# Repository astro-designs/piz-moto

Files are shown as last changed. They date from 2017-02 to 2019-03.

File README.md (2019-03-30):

PiZMoto
=======
A code library for the PiZ-Moto / PiZ-Moto+ add-on board for the Raspberry Pi Zero
with assembly instructions, examples for both Python & Scratch, tutorials,
and a 3D printable design for a Raspberry Pi Zero powered MicroPiNoon compatible balloon-popping 'bot!

The PiZ-Moto is a self-assembly simple 2-channel motor controller with extras...
   * On-board 5V power supply to power the Raspberry Pi Zero from the motor power supply
   * 3-pin connector for adding an infra-red reflective 'Line Follower' sensor
   * 4-pin connector for adding a HC-SR04 ultra-sonic distance sensor
   * 2 x 3-pin servo-compatible connectors usable as inputs or outputs (for LEDs, servos, etc.)
   * on-board GPIO driven LED
   * Expansion header bringing out some spare GPIO
   * Compatible with the CamJam EduKit-3 available from www.thepihut.com

Installation instructions for the Raspberry Pi
**********************************************

These instructions assume you are using the latest version of Raspbian and have logged in as user "pi"
Last tested with Raspbian Stretch 2017-09-07

1) Run git clone to clone the piz-moto folder to users/pi

   cd ~
   
   git clone https://github.com/astro-designs/piz-moto.git
   
2) Run the setup program

   sudo python setup.py install
   
This completes the basic installation.

Using a PS3-compatible wireless controller
******************************************

These setup notes are based on: https://www.piborg.org/blog/rpi-ps3-help

sudo apt-get update

sudo apt-get -y install libusb-dev joystick python-pygame

cd ~

wget http://www.pabr.org/sixlinux/sixpair.c

gcc -o sixpair sixpair.c -lusb

Tested with a Rock Candy wireless PS3 controller and one other ultra-cheap wireless PS3 controller found on ebay.

If you're looking for a wireless PS3 controller, this is also worth a look, available from The PiHut although i've not tested it myself...
https://thepihut.com/products/raspberry-pi-compatible-wireless-gamepad-controller

Documentation
*************

Assembly instructions: 
                     docs/PiZ-Moto+ Instructions.pdf (Instructions for PiZ-Moto+ (black)
                     docs/PiZ-Moto Instructions.pdf (Instructions for PiZ-Moto (green)

Example Code
************
examples/ps3bot.py - Simple 2-wheeled robot controller using a wireless PS3 controller

examples/wiibot.py - Simple 2-wheeled robot controller using a Bluetooth WiiMote controller
                     Includes routines to follow lines using an infra-red reflective sensor
                     and avoid objects using a HC-SR04 range sensor
                     
examples/candle.py - Using a PiZ-Moto motor driver to drive a lamp to simulate a flickering candle
                     
examples/Scratch/EduKitRobot.sb - Scratch based example,
                     Ideal for getting to grips with motor control using Scratch on the Raspberry Pi
                     VNC into your Raspberry Pi & PiZ-Moto and run Scratch over VNC to control your robot
                     instead of using a PS3 or Wii controller

Tutorials
*********

These tutorials were written for a simple motor control tutorial held at the Cotswold Raspberry Jam
in June 2017. The tutorial worksheet can be downloaded from:
http://cotswoldjam.org/downloads/2017-06/motor-control-worksheet.pdf

tutorial/task1.py
tutorial/task2.py
tutorial/task3.py

3D Printable MicroPiNoon 'Bot
*****************************

We've included all files, including STL files and the Sketchup model for our 3D-printed MicroPiNoon
MicroPiNoon compatible balloon-popping robots. These are a regular feature at the Cotswold Raspberry Jam

MicroPiNoon/3D_Printing         - stl files
MicroPiNoon/Bot4.jpg            - Simple render of the completed robot
MicroPiNoon/Instructions.txt    - Assembly instructions
MicroPiNoon/PartsList.txt       - List of parts needed for the robot

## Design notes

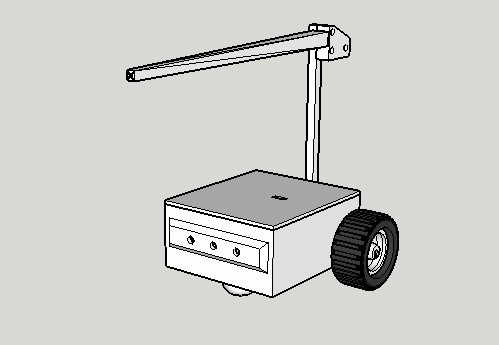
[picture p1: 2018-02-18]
MicroPiNoon/Bot4.jpg

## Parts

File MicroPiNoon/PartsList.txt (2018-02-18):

Parts list for Micro-Pi Noon fighting robot
*******************************************

1) Raspberry Pi Zero, Zero W, Zero WH Note: Header needs to be fitted. (Works with any revision / version)
2) PiZ-Moto motor controller board / kit;
3) Motors - 50:1 or 298:1 micro geared 6V motor.
   https://shop.pimoroni.com/products/micro-metal-gearmotor-extended-back-shaft
   or similar
4) PP3 Battery clip with wires attached
   https://shop.pimoroni.com/products/pp3-battery-snap
   or similar
5) Battery holder
   http://uk.farnell.com/keystone/2476/battery-holder-a-aa-snap-in/dp/2293271?st=aa%20battery%20holder%204
   or similar
6) M3 x 20 pan head screw (x4)
7) M3 full nut (x4)
8) A pin
   approx 20mm long with the head cut off. A small cork is recommended for safety...
9) Wheels - Polulo are good for these:
   https://shop.pimoroni.com/products/pololu-wheel-42x19mm-pair
   https://shop.pimoroni.com/products/moon-buggy-wheels-pair
   https://shop.pimoroni.com/products/pololu-wheel-32x7mm-pair
10) 8GB micro SD Card
11) Wireless PS3 controller
    Rock Candy or similar work well.

Note:
You will also need:

Insulated wire to solder to the micro motors.
   About 4 lengths of 10cm, preferably two in one colour and two in a different colour
   More may be needed if you opt for using a switch (see optional items below) to switch the power on/off.

3D printed parts:
*****************

1) BOT4 Chassis.stl - This is the main chassis;
2) BallFoot.stl - This is the non-rotating simple ball-castor alternative used to support the front of the 'bot';
3) BalloonMast.stl - this is the pole at the back of the bot that holds the baloon;
4) BalloonHolder.stl - this is the quick-release balloon holder;
5) Spike - this is the arm that extends forward over the 'bot' and carries the pin;
6) SpikeHolder.stl - this is a small clamp that holds the spike and baloon holder onto the baloon mast;
7) Bot4_Lid.stl - this is a simple clip-on lid that can act as a cover over everything. 

Optional:
a) Polulo #953 metal ball-castor. Optional replacement for 3D printed solid non-moving front 'foot'
   https://shop.pimoroni.com/products/pololu-ball-caster-with-3-4-metal-ball

b) Sliding power switch
   http://uk.farnell.com/knitter-switch/mfs131d/switch-spdt-0-35a-30vdc-solder/dp/219459?st=Slide%20switch
   or similar (check dimensions match the slide switch hole on the 'BOT4' 3D printed chassis

Tools required:
***************

1) Soldering iron - a good one with a fine tip. Suitable for lead-free solder
   Lead-free solder. Reasonably fine 0.5mm - 1mm

2) Screwdrivers to match the screws used
3) M3 spanner or nut-spinner - or a pair of pliers...
3) Cutters, pliers

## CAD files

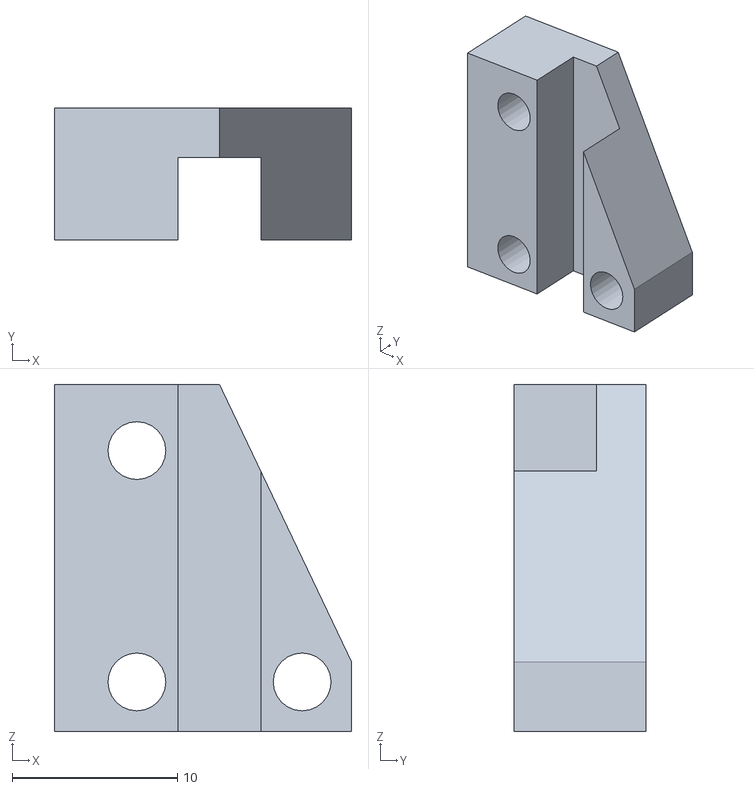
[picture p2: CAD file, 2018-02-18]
MicroPiNoon/3D_Printing/SpikeHolder.stl
18.0 x 8.00 x 21.0

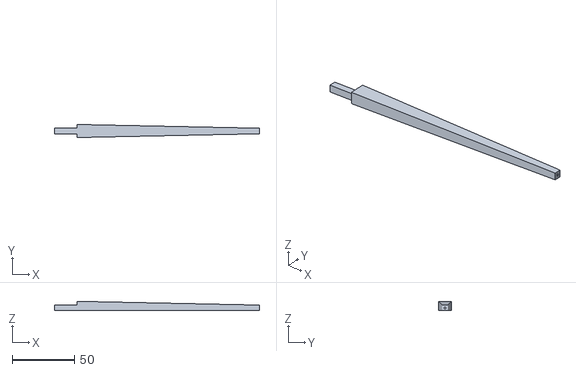
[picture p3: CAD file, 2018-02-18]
MicroPiNoon/3D_Printing/Spike.stl
165.0 x 10.5 x 7.50

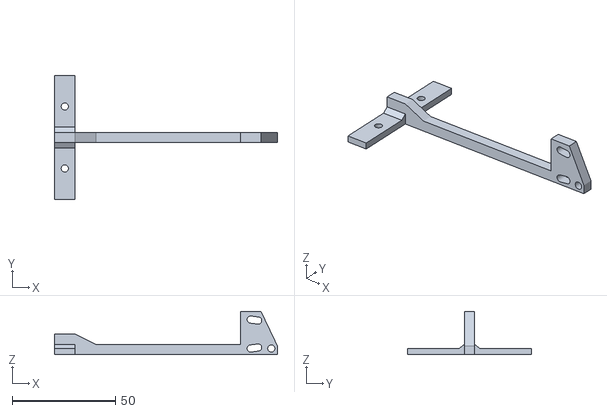
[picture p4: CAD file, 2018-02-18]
MicroPiNoon/3D_Printing/BalloonMast.stl
108.0 x 60.0 x 21.0

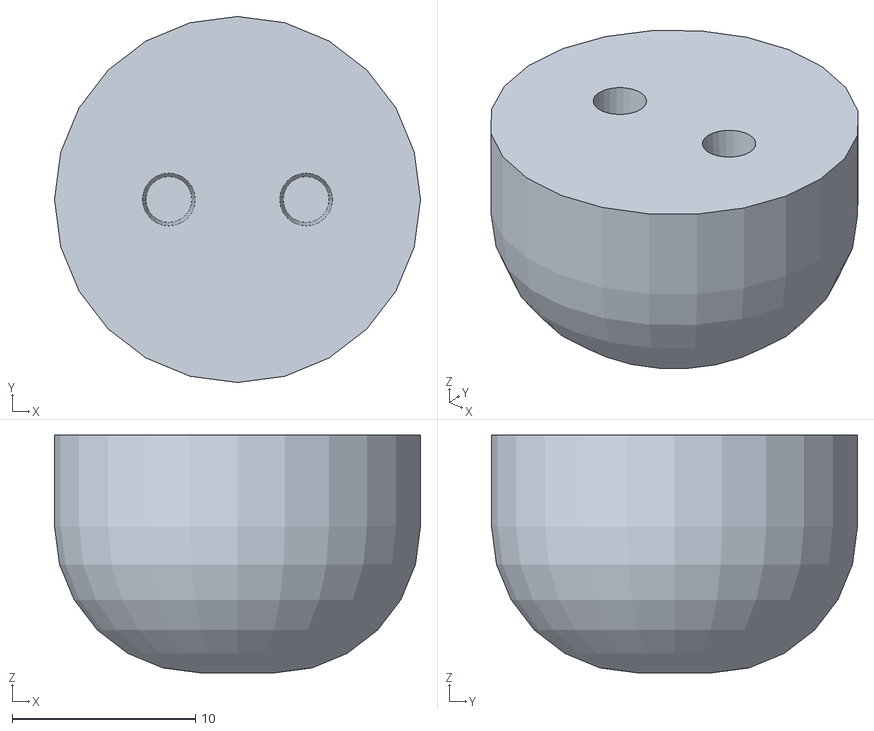
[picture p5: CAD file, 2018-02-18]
MicroPiNoon/3D_Printing/BallFoot.stl
20.0 x 20.0 x 13.0

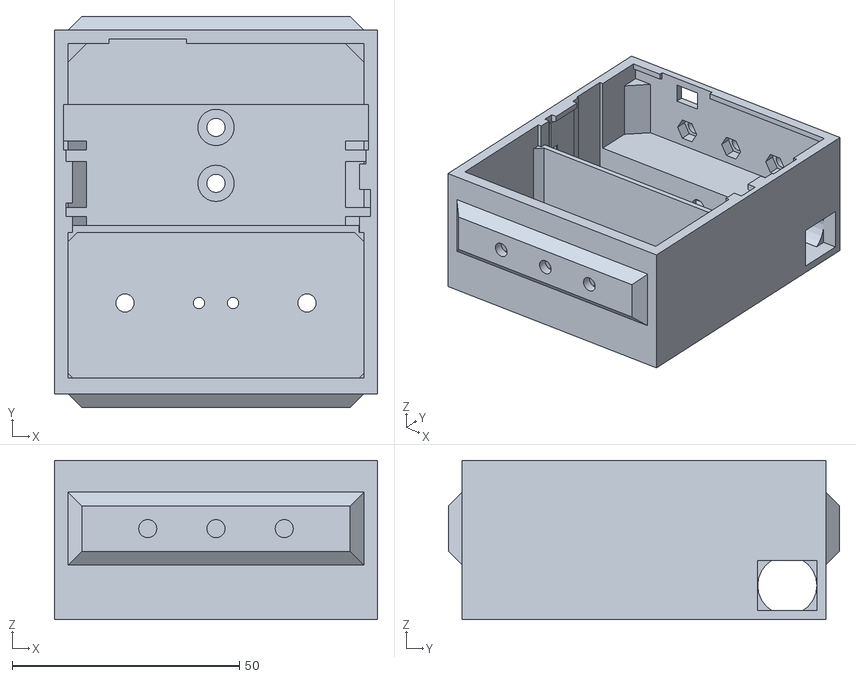
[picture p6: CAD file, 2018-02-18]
MicroPiNoon/3D_Printing/Bot4Chassis.stl
71.0 x 86.0 x 35.0

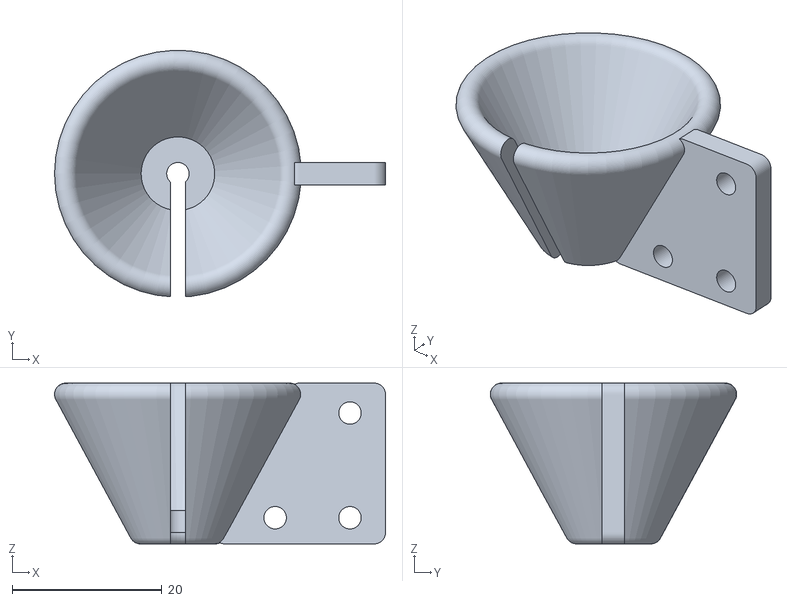
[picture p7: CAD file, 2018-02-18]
MicroPiNoon/3D_Printing/BalloonHolder.stl
44.2 x 32.9 x 21.5

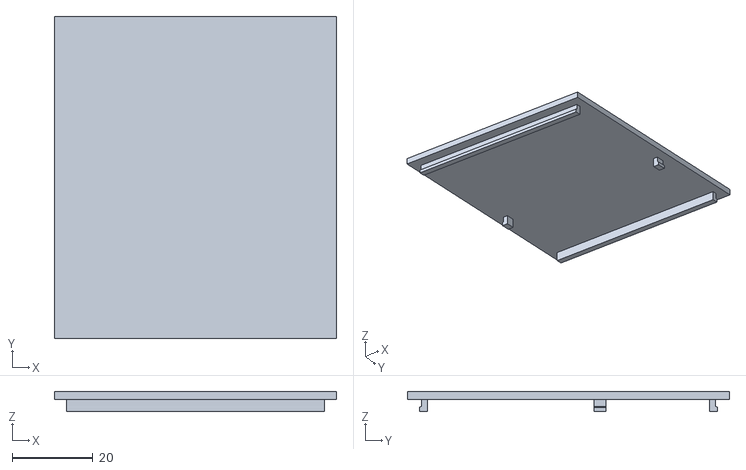
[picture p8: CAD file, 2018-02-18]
MicroPiNoon/3D_Printing/Bot4Lid.stl
70.0 x 80.0 x 5.00

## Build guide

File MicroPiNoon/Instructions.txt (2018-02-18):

Work in progress...

1) Print the components that make up the 'Bot4' chassis and parts

2) Solder wires to the motors
   Pass the motor wires through the holes in the side and out of the fiddly small hole inside
   Glue the motors in place, taking care not to get any glue on the gears. Recommedn a small qty of rapid-set epoxy resin glue or hot-melt glue.
   Note - make sure the motor wires are long enough to connect to the motor driver board once it's all assembled.

3) Glue the BallFoot onto the front section of the base of the chassis. There are two holes that line up with two holes in the BallFoot, these can be used to screw the ball foot in place using M2 x 6mm pan-head screws. A little glue may be needed to glue the screw threads into the BallFoot part as there is no thread.

4) Glue the slide switch (optional part) onto the back of the 'Bot4' chassis so that the switch protrudes out through the hole in the back and can slide fully both ways. I recommend rapid-set 2-part epoxy resin glue or hot-melt glue.

5) (optional - if using the slide switch) Solder the red wire from the battery clip to the centre pin of the slide switch

6) (optional - if using the slide switch) Solder a second red wide from one of the outer terminals of the slide switch

7) Screw the red wire from the slide switch (if using the switch) or the red wide from the batter clip (if not using the slide switch) to the positive battery terminal on the PiZ-Moto motor driver.

8) screw the black wire from the battery clip to the negative battery terminal on the PiZ-Moto motor driver.

9) Screw the motor wires to the two pairs of motor terminals on the PiZ-Moto board. Check the PiZ-Moto instructions for information on which conenctor to use for which motor.

10) Solder the 40-pin header onto the Raspberry Pi if it's not already fitted.

11) Plug the PiZ-Moto into the Raspberry Pi.

12) Assemble the Raspberry Pi with the PiZ-Moto driver board into the Bot4 chassis.

13) Plug the SDCard into the Raspberry Pi

14) Plug the wireless dongle for the PS3 controller into the Raspberry Pi USB port.
    Alternatively, plug a Bluetooth 'dongle' into the Raspberry Pi USB port if using a WiiMote or other Bluetooth based controller

15) Push the wheels onto the motors...
    Note: It's sometimes easier to test the Bot without the wheels attached. That way it won't roll itself off the table if you accidentally get the controls wrong...

16) Connect the battery...

At this point, what happens next depends on what's on your SD Card... If you're working from a fresh installation of Raspbian then there's probably some further setup required and you'll probably need to connect a monitor to the Raspberry Pi.

But if it's all ready to go and you run the ps3bot.py program at boot-up then after about 60s you should be able to press the home key on the PS3 controller and you should have control of the Bot.

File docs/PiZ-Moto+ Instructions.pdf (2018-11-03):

# PiZ-Moto+

(Pronounced “Pie-Zee Moto Plus”)

## Assembly Instructions (1.0)

Developed for the Cotswold Raspberry Jam (@CotswoldJam)

Latest instructions available at:

https://github.com/astro-designs/piz-moto

Introduction

The PiZ-Moto kit is designed for use with the Raspberry Pi ‘Zero’. It is based around the Texas Instruments L293DNE quad half-bridge driver which can be used to control up to two motors in two directions. The L293DNE was chosen because it’s pretty much the only low-cost motor driver you can find that’s ‘through-hole’ not surface-mount making it ideal for a self-assembly kit like this. We wanted to make this motor driver a little different from others, after all there are quite a few available. So what makes this one different? Firstly, it includes a built-in 5-volt regulator that enables the power source that’s used to power the motors to also power the Raspberry Pi Zero. Secondly, it includes interfaces for an infra-red reflecting sensor, an ultra-sonic range sensor and a couple of 3-pin interfaces that support LEDs, low-power radio-control style servos or general purpose I/O. Plus, we’ve also brought out 8 other spare GPIO pins from the Raspberry Pi’s GPIO header to an 8-pin header. For the 5-volt power supply we chose a low-cost leaded low drop-out linear regulator. Being low drop-out means that the motor power supply voltage only needs to be approximately 0.5V greater than the 5V supply needed by the Raspberry Pi. A 4-cell AA battery pack which produces 6V, makes an ideal power source for this motor driver kit. With the motor driver, 5-volt regulator and the extra simple but versatile interfaces on the board, the PiZ-Moto makes it easy to build an intelligent line-following, object avoiding 2-wheel robot using the Raspberry Pi Zero. The final feature of this particular design is that it’s fully compatible with the CamJam EduKit #3 so if you’ve already got software that works with the EduKit #3 then it’ll work with the PiZ-Moto too.

And another thing, in this latest version, we’ve also added a 3-pin power supply header that, together with the 8-pin spare GPIO header, it allows you to stack a second, slightly modified PiZ-Moto+ board on top of the first to double the number of motors that can be driven.

Contents

In your kit, you should find:

1) PiZ-Moto+ PCB (x1)
2) 100 Ohm Resistors (x4)
3) 1.8k Ohm Resistors (x2)
4) 3.3k Ohm Resistors (x2)
5) BA50BCT (or similar) Low-dropout Linear Regulator (x1)
6) L293DNE Quad Half-Bridge Driver I.C. (x1)
7) I.C. Socket (x1)
8) 2-way Screw Terminal (x3)
9) 3mm green LED (x2)
10) 24-way Pin Header (x1)
11) 22uF 16V Aluminium Electrolytic Capacitors (x2)
12) 40-way Socket (x1)

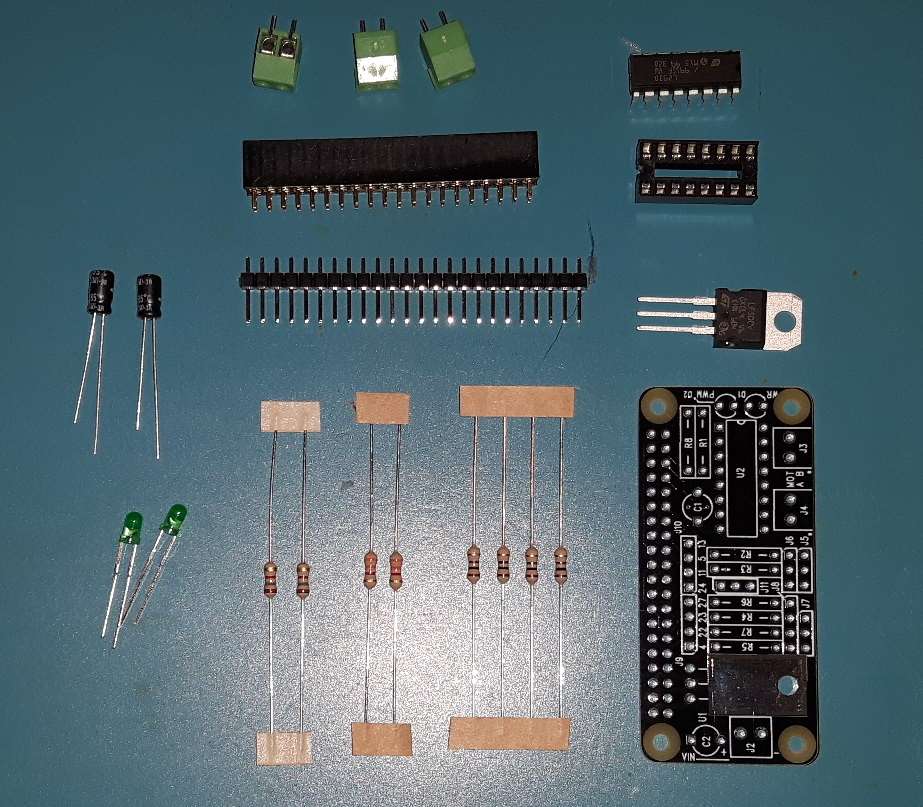
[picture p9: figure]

Contents of the PiZ-Moto+ Kit

Tools Required

1) A reasonably decent soldering iron
2) Solder wire
3) A pair of snips
4) A pair of snipe-nosed Pliers
5) Optionally, a solder pult de-soldering tool or solder wick in case you need to remove any components or clean up any solder.

Assembly Instructions

Right, let’s get stuck in…

1) It’s always best to start with the smallest components so firstly we’ll fit the resistors, then gradually move through the taller components. There are three different values of resistors used so let’s fit these in turn.
a. Firstly, fit the four x 100 ohm resistors.
These are colour-coded BROWN-BLACK-BROWN [GOLD]

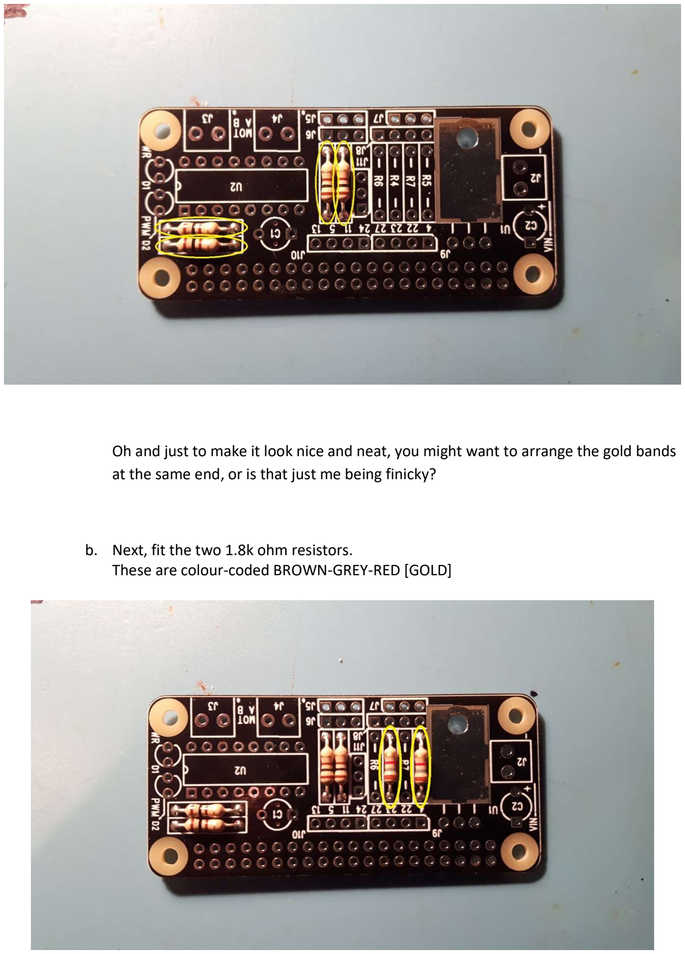
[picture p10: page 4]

Oh and just to make it look nice and neat, you might want to arrange the gold bands at the same end, or is that just me being finicky?

b. Next, fit the two 1.8k ohm resistors.
These are colour-coded BROWN-GREY-RED [GOLD]

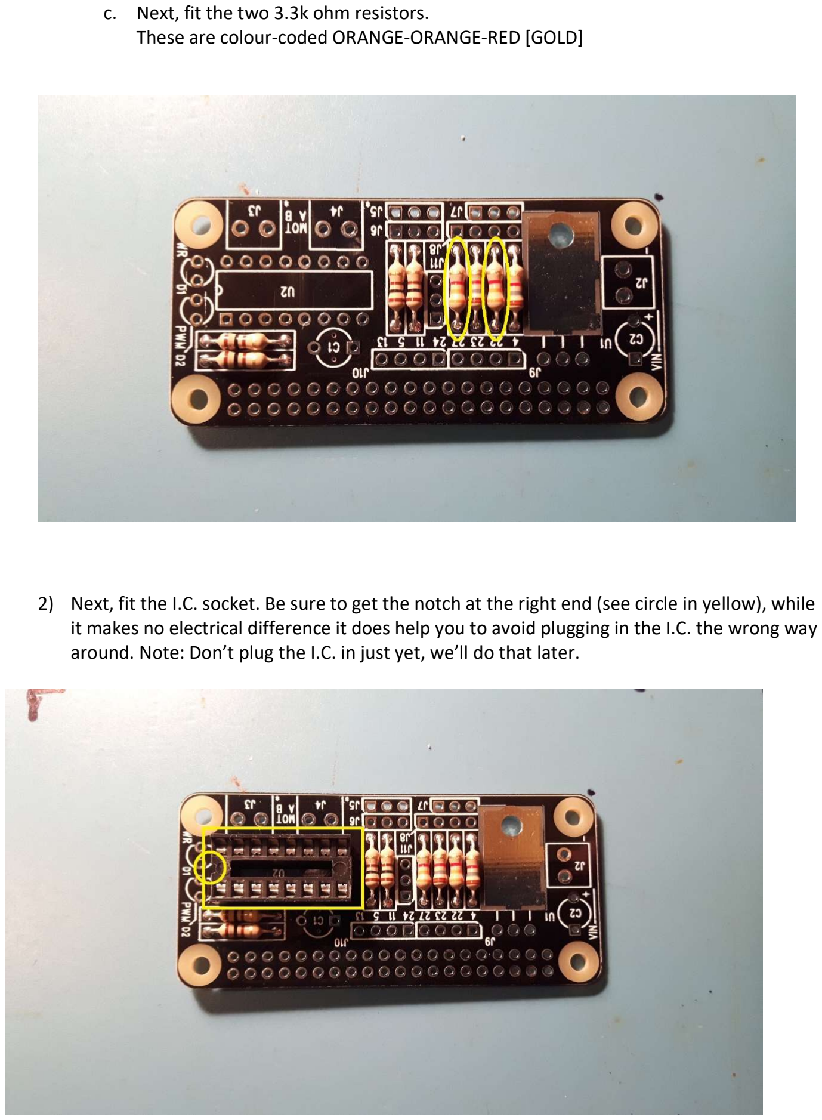
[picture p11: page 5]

c. Next, fit the two 3.3k ohm resistors.
These are colour-coded ORANGE-ORANGE-RED [GOLD]
2) Next, fit the I.C. socket. Be sure to get the notch at the right end (see circle in yellow), while it makes no electrical difference it does help you to avoid plugging in the I.C. the wrong way around. Note: Don’t plug the I.C. in just yet, we’ll do that later.

3) Next it’s the turn of the linear regulator:

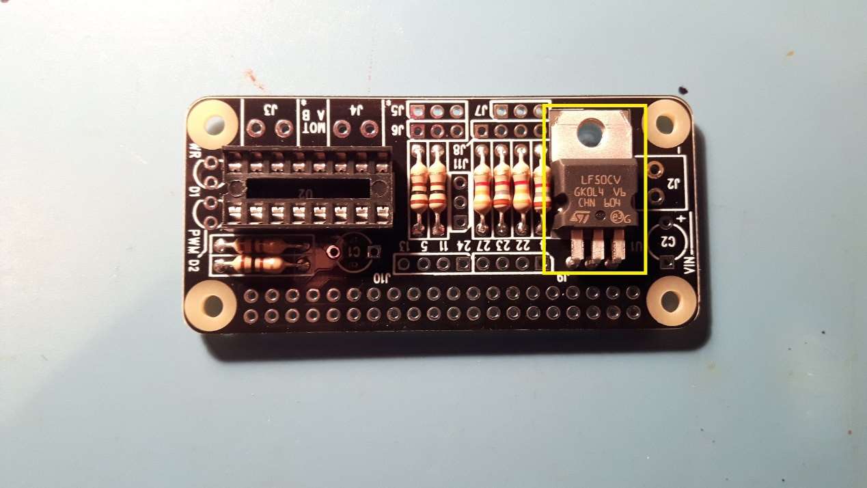
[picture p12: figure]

The linear regulator is supplied without the leads bent into position so these must be carefully bent. To get the mounting hole in the regulator to line up correctly, the leads must be bent just a fraction above the shoulder, where the leads get slightly wider (see picture below).

Note – if you prefer to power the motors separately from the Raspberry Pi which does have the advantage that you can then run the Motors at up to 36V, then simply don’t fit the linear regulator. See the note in the FAQ section on powering the motors separately from the Raspberry Pi.

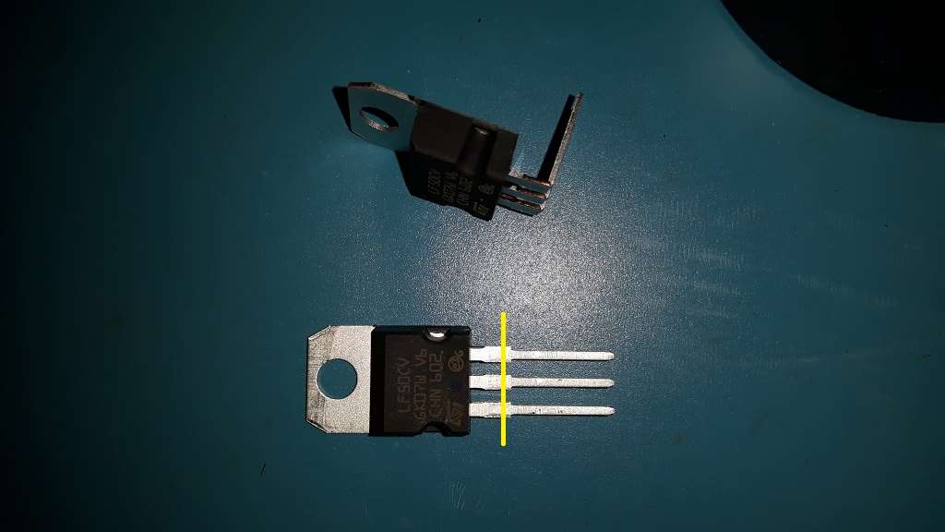
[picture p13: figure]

4) Fit the LEDs:
Ensure that the LEDs are fitted the correct way around. The ‘cathode’ terminal is indicated by the shorter lead. The circle outline for the LED has a flat section to mark the ‘cathode’, also marked with the yellow arrow in the picture below. Note: If the leads have been cropped and you want to identify the ‘cathode’, take a close look at the inside of the LED, the cathode is always the larger of two electrodes.

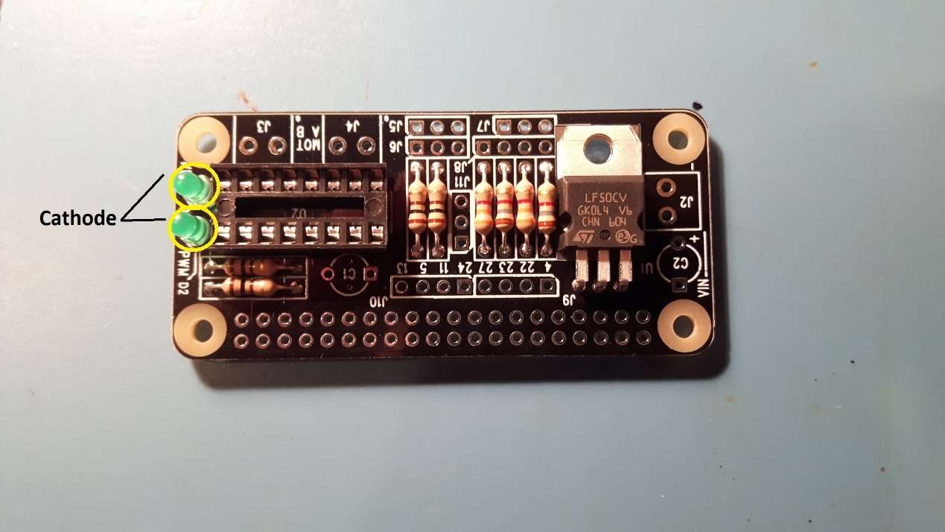
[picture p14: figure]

5) Next, fit the two capacitors. Firstly, these need to have the pins ‘formed’ slightly to match the separation of the holes on the board. The pins should be separated by about the same amount as the diameter of the capacitor. See the additional picture below illustrating how they should look. Secondly, it’s important to note that these are polarised capacitors so they MUST be fitted the correct way around. The negative terminal is marked on the capacitor with a stripe and “-“ symbols. The arrows on the picture below point to where the negative terminal should go. One of the terminals for the capacitor shape on the PCB has a square pad, this corresponds to the positive lead on the capacitor. Please note that the capacitors supplied in the kit may be slightly different to the ones shown in the bottom picture below.

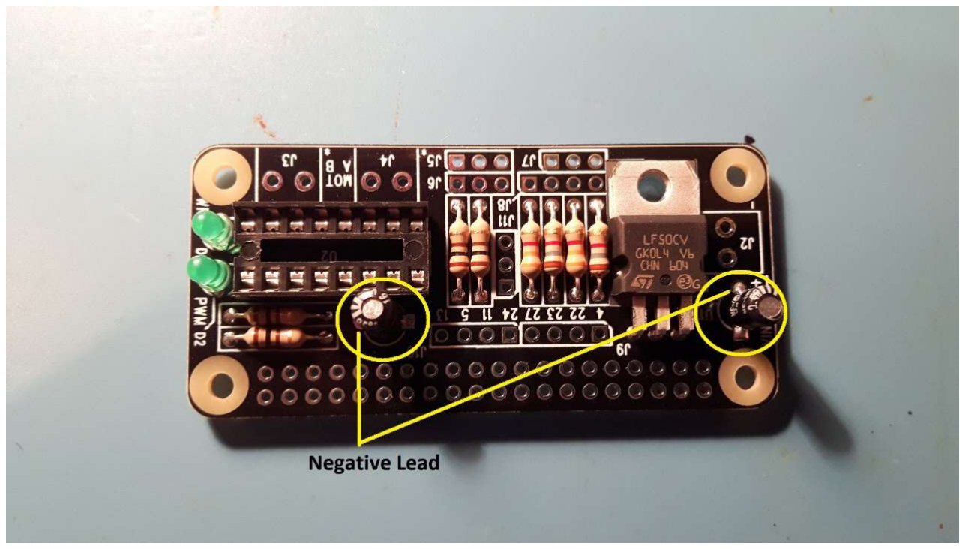
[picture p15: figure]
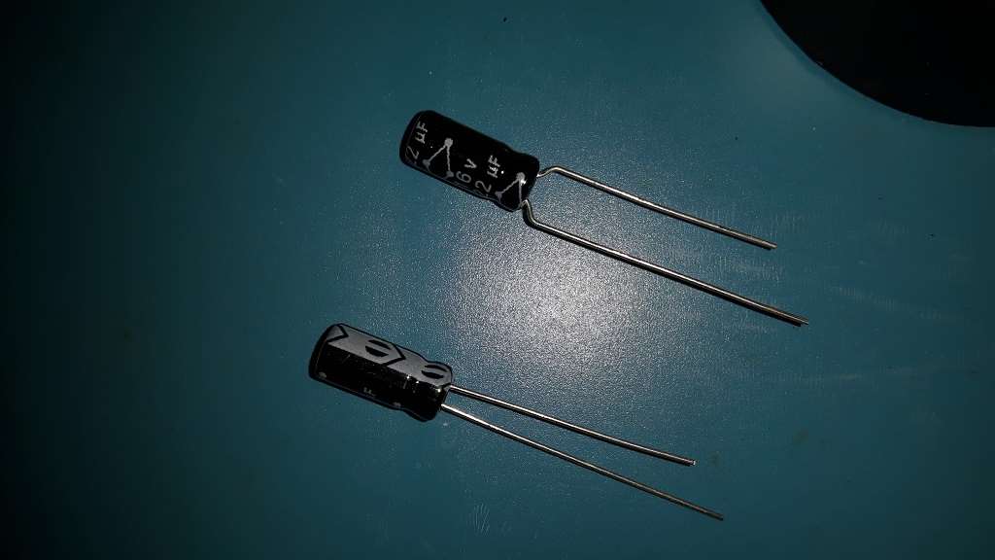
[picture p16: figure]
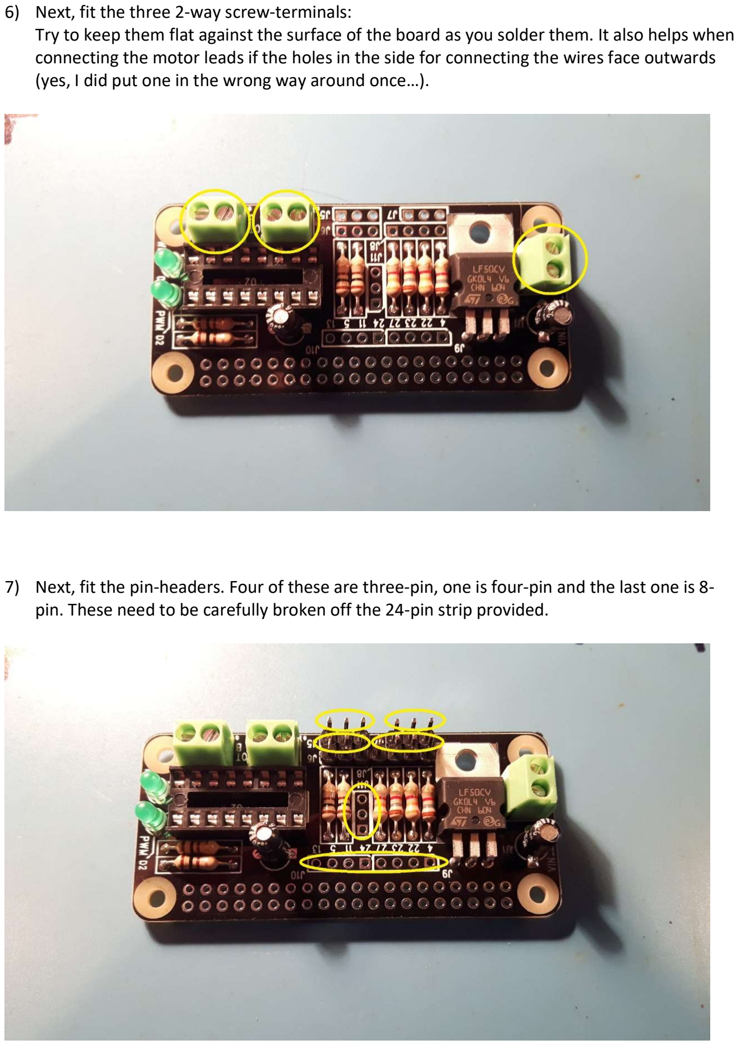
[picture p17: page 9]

6) Next, fit the three 2-way screw-terminals:
Try to keep them flat against the surface of the board as you solder them. It also helps when connecting the motor leads if the holes in the side for connecting the wires face outwards (yes, I did put one in the wrong way around once…).
7) Next, fit the pin-headers. Four of these are three-pin, one is four-pin and the last one is 8-pin. These need to be carefully broken off the 24-pin strip provided.

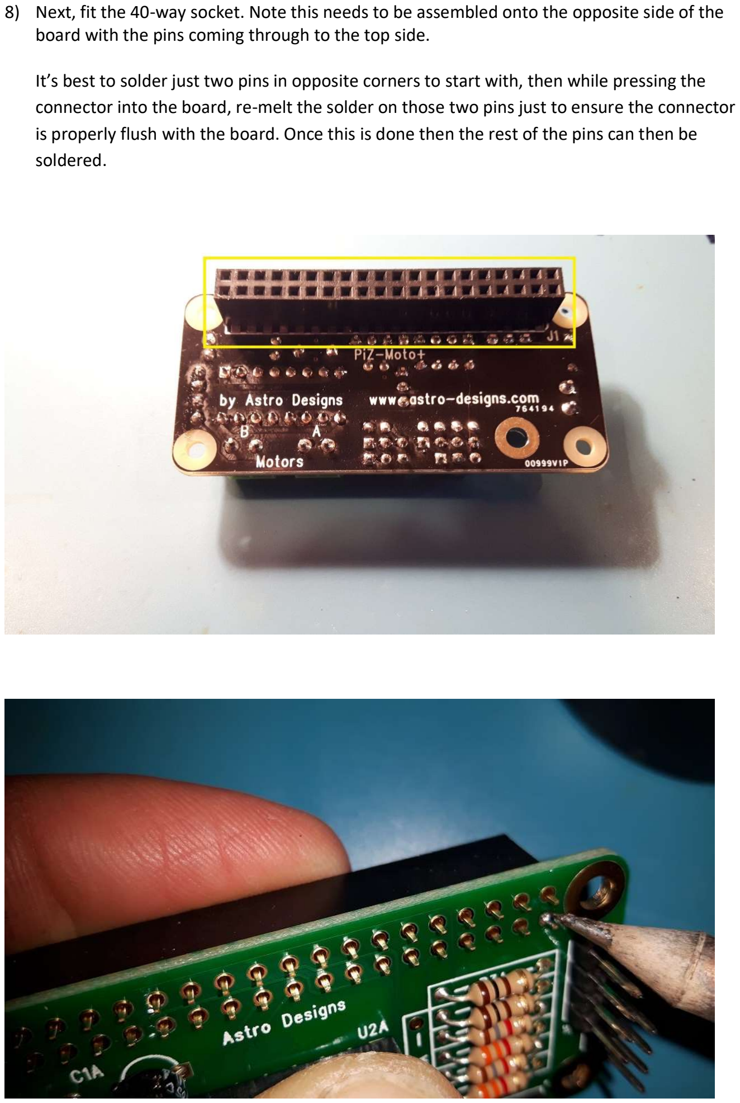
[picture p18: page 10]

8) Next, fit the 40-way socket. Note this needs to be assembled onto the opposite side of the board with the pins coming through to the top side.

It’s best to solder just two pins in opposite corners to start with, then while pressing the connector into the board, re-melt the solder on those two pins just to ensure the connector is properly flush with the board. Once this is done then the rest of the pins can then be soldered.

9) That’s it! Ok, you should now do a quick check to ensure that all components are fitted and are fitted correctly. Check:
a. All components are fitted;
b. All pins are soldered cleanly;
c. All long-leads have been snipped-off;
d. The I.C. socket is fitted the correct way around;
e. Capacitors are fitted the correct way around;
f. The LEDs are fitted the correct way around;
10) Finally, plug the L293DNE motor driver I.C. into the I.C. socket. Make sure it’s fitted the correct way around, the notched end should appear next to the LEDs.

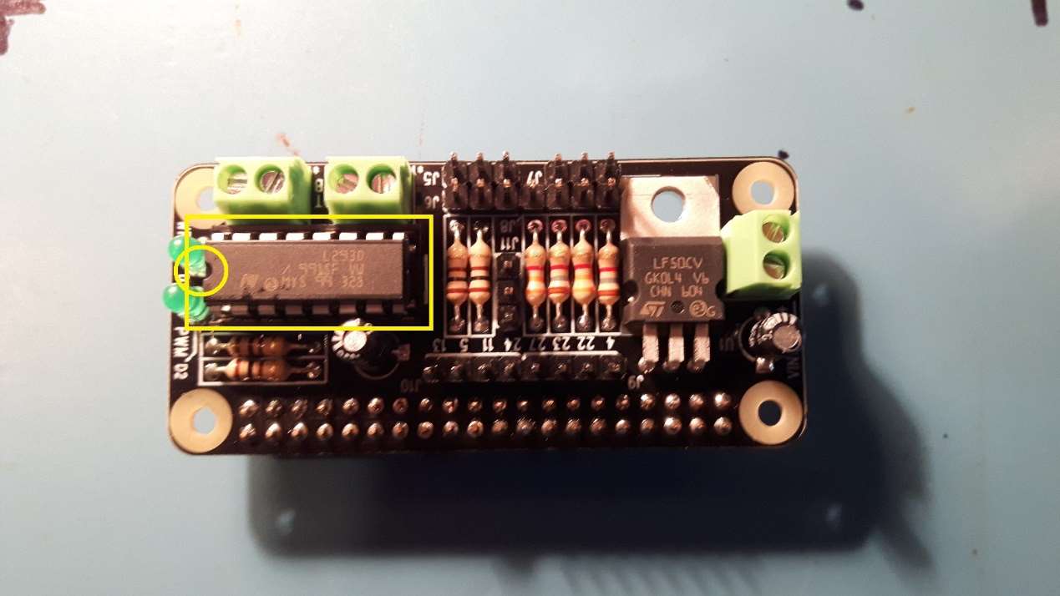
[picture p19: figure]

Connecting the Motors

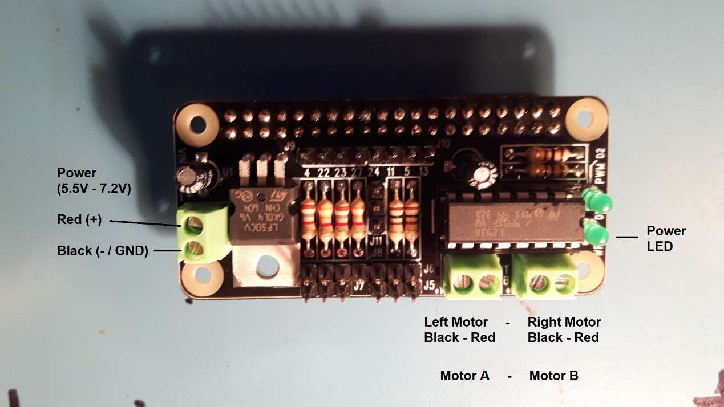
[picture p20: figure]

Each pair of screw terminals above connects to a single motor. In theory you could connect two motors in parallel to use four motors, with two motors on a single screw terminal but start with one motor per screw terminal pair. The motor driver is rated to 600mA per motor. The connections shown above are completely compatible with the CamJam EduKit #3.

Connecting the Power Supply or Battery:

It’s important to get the polarity correct when connecting the battery. Getting this wrong could damage the board. The ground / black / 0V wire from the battery should connect to the battery screw terminal that’s closest to the corner of the board (marked in yellow as “-“ in the picture below). The positive / red wire from the battery should connect to the other screw terminal, marked below in yellow as “+”.

It’s best to have a switch in line with your battery so that it’s easy to turn things off. Make sure the switch is off when connecting the battery to the board.

Important note: The PiZ-Moto is designed to be powered through the screw-terminal power connector. The PiZ-Moto uses an on-board 5V regulator to provide a 5V regulated power supply to the Raspberry Pi Zero through the Pi’s +5V & GND pins on the Pi’s GPIO connector. Please do not power the Pi through the Pi’s USB power connector while connected to the PiZ-Moto. While this is unlikely to result in any damage, you will not be able to provide power to the motors using the Pi’s USB power connector so it’s recommended that you don’t use that connector when using the PiZ-Moto.

It’s designed to run off four “AA” cells which should provide approximately 6V. But it will work on as little as 5.5V. The recommended upper limit is 7.2V although it will tolerate more. How much it can tolerate comes down to how much current is needed by the Pi Zero. If you connect a USB WiFi dongle or a camera then I wouldn’t recommend anything more than 6V. Also check the temperature of the regulator (U1A) as this gets hot if the Pi Zero draws more current.

It’s really best suited to minimal applications where the loading on the Pi Zero is very little. A Bluetooth dongle or Wireless Keyboard Dongle consumes very little power so these are ideal.

One final note on the battery side of things, you don’t need to (& shouldn’t) power the Pi Zero separately. The Pi Zero is powered from the regulator on the PiZ-Moto.

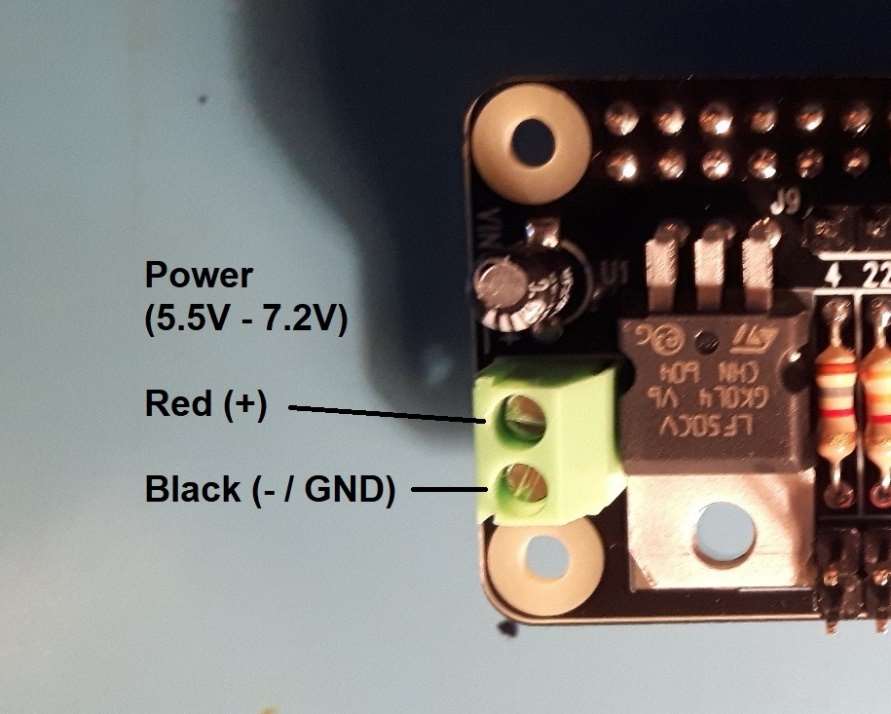
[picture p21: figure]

Connecting the Photo Sensor

The Photo Sensor header is designed to connect directly to a photo-reflector / line sensor like the one found in the CamJam EduKit #3. Simply connect the three pins on the PiZ-Moto Photo Sensor Header to the three pins on the photo-reflector / line sensor, making sure you get the pins connected to the right terminals on the photo-reflector board and you’ll be ready to test.

Please note that the ordering of the pins on the PiZ-Moto board are different to the order of the pins on the line sensor found in the EduKit #3 so please take care when connecting the sensor.

The signal connection on the PiZ-Moto Photo Sensor Header can also be used as a general-purpose 5V input and is connected to the Pi Zero’s GPIO-25 pin via a 5V to 3.3V level shifting network.

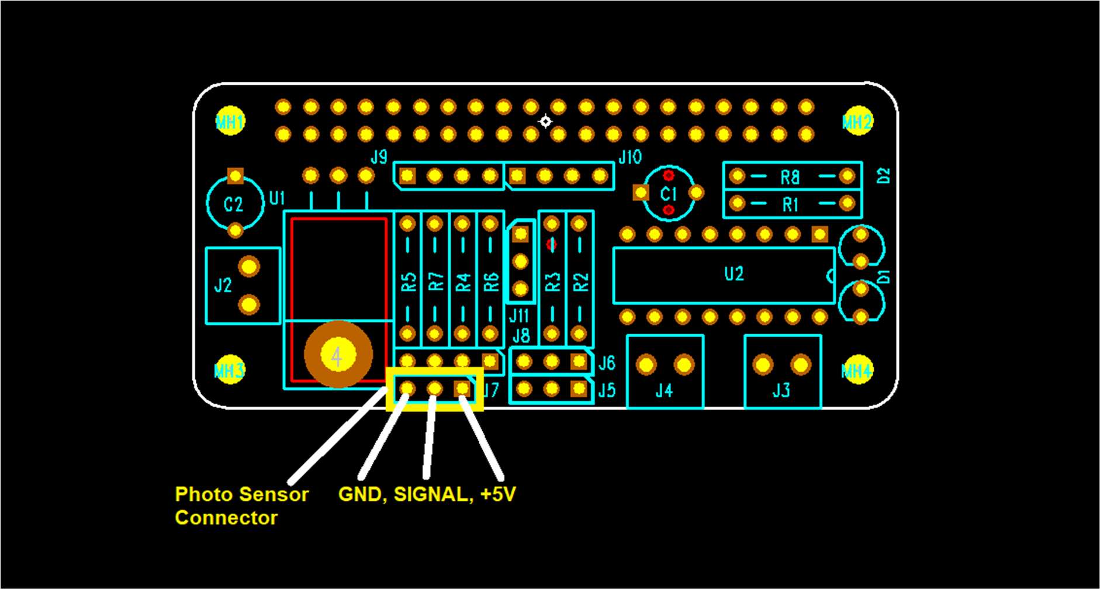
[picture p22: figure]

Connecting the Range Sensor

The Range Sensor header is designed to connect directly to an SR-04 range sensor, as found in the CamJam EduKit #3. The SR-04 is also available separately from several suppliers. Simply connect the four pins on the PiZ-Moto Range Sensor Header to the four pins on the SR-04, making sure you get the pins connected to the right terminals on the SR-04 and you’ll be ready to test.

The ‘Echo’ connection on the PiZ-Moto Photo Sensor Header can also be used as a general-purpose 5V input and is connected to the Pi Zero’s GPIO-18 pin via a 5V to 3.3V level shifting network. The ‘Trig’ connection can be used as a general-purpose 3.3V input or output and is connected directly to the Pi Zero’s GPIO-17 pin.

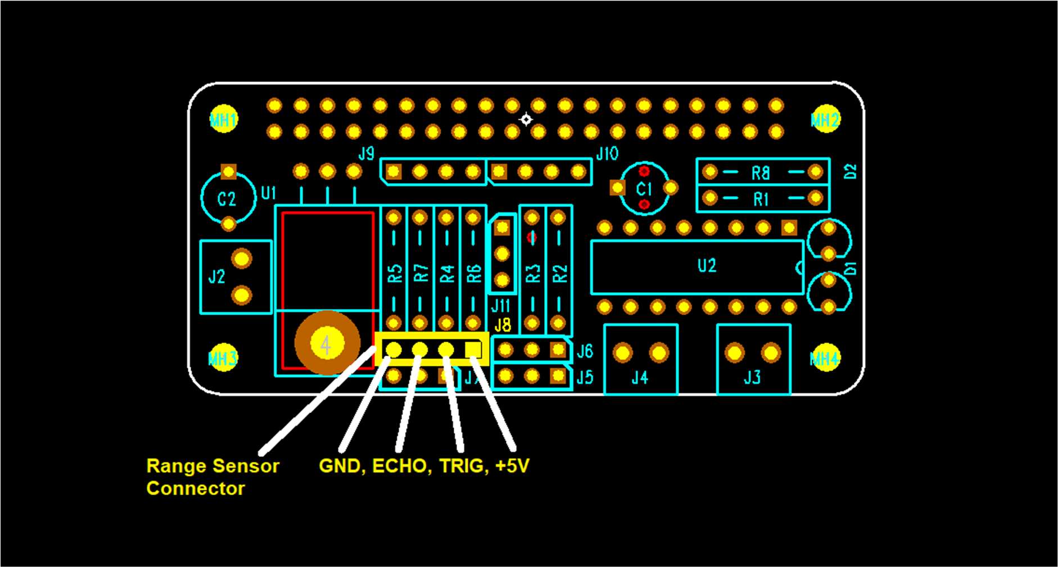
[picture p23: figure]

Connecting the LEDs or Servos

The LED header is really a couple of general purpose I/O pins, each paired with it’s own ‘GND’ pin. The two LED pins have a 100 ohm resistor in series with it’s connection the header on the Pi Zero. This both protects the I/O on the Pi Zero as well as allowing an LED to be connected directly across the two pins with no need for an extra resistor in line with the LED. In our examples here, we just connect a couple of LEDs directly but you could use these pins as inputs or outputs.

The LED1 / Servo1 Signal connection on the LED Header is connected to the Pi Zero’s GPIO-16 pin via a 100 ohm resistor. The LED2 / Servo2 Signal connection is connected to the Pi Zero’s GPIO-19 pin via a 100 ohm resistor. Note that GPIO-16 can be configured as PWM0 on the Raspberry Pi which means that a servo on this connector can be driven by a ‘Hardware PWM’ signal instead of a software based PWM signal. This means the servo position will be more accurate, less ‘noisy’ and it also means that this connector can be configured to drive Neopixel RGB LED strings.

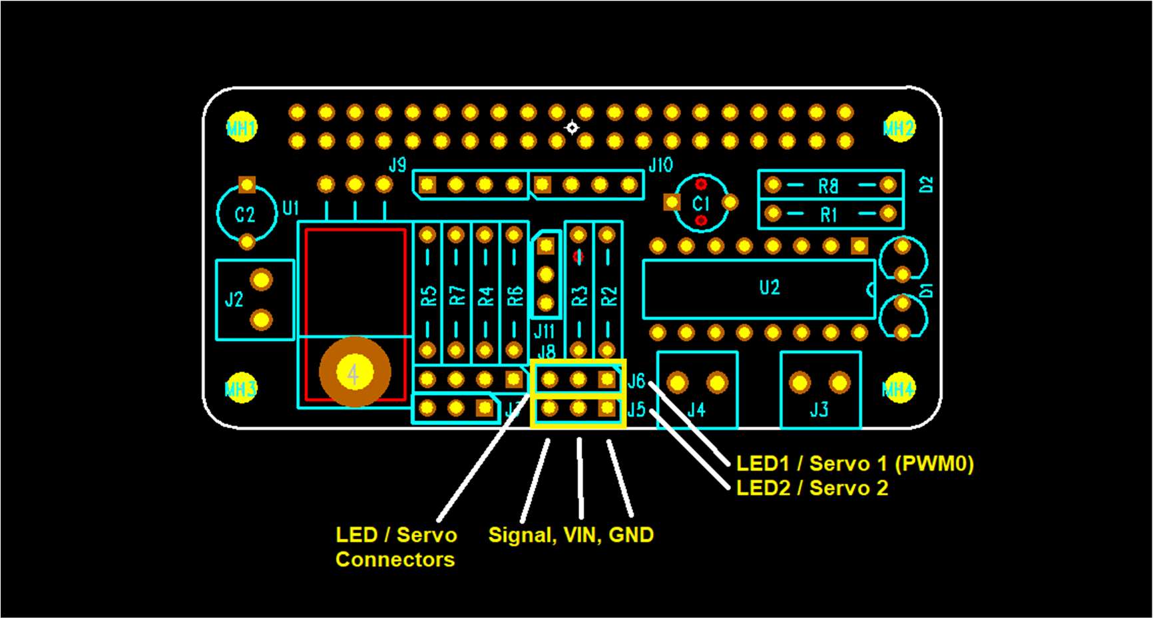
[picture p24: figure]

The On-board LED

We’ve added an on-board LED to this later version of the PiZ-Moto because we found that this is particularly useful to use as a status indicator when running the PiZ-Moto+ & Raspberry Pi in headless mode. The on-board LED is located next to the Power LED.

The on-board LED is connected to and can be controlled using GPIO-6 (BCM) on the Raspberry Pi

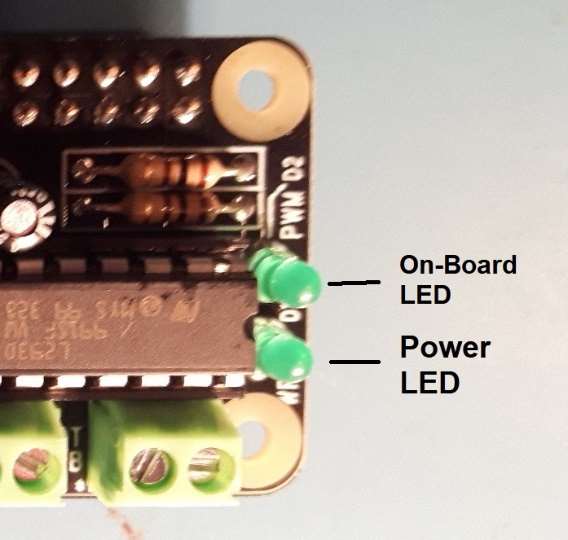
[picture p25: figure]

Expansion

There are additional pin headers on the PiZ-Moto+ to provide access to power and other GPIO pins on the Raspberry Pi. This provides limited support to allow you to connect other functions to the Raspberry Pi with a PiZ-Moto+ fitted to it.

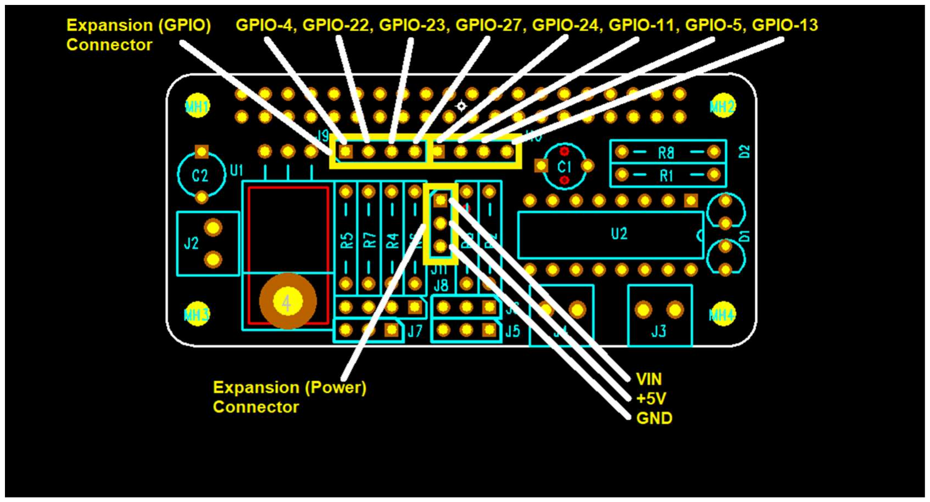
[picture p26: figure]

Testing

1) Firstly, without connecting the PiZ-Moto+ to the Raspberry Pi, connect the power supply or battery and switch it on (if there’s a switch), making sure that you get the polarity of the power supply correct!
2) Check that the Power LED comes on. If it doesn’t turn it off immediately and double-check the polarity of the power supply;
3) If you have a volt-meter, measure the voltage on the “+5V” terminals of the 40-way socket. These should be very close to 5.0V. You can also measure this across the Photo Sensor connector or Range Sensor connector – see the pictures earlier on in this document to identify which pin is GND and which pin is +5V;
4) Disconnect the power supply or battery and check that the LED goes off;
5) Connect the PiZ-Moto to a Raspberry Pi Zero. Take care to ensure that the connector lines up correctly and is not offset by (say) one pin. (I’ve done that once and now have a PiZero that’s minus one GPIO output )
6) The Python script PiZ-Moto+_test.py is the best way to test the board. If you connect the battery, motors, LEDs, line sensor & proximity sensor and run the script, it’ll quickly exercise all functions on the PiZ-Moto allowing you to check it all works. You’ll need a Pi Zero with HDMI display & USB keyboard connected.
a. Plug a small DC brushed motor into each motor terminal;
b. Connect the 3-pin photo sensor header to a photo-reflector / line detector;
c. Connect the 4-pin range sensor header to a SR-04 ultrasonic range sensor;
d. Connect the LED / Servo headers to a couple of LEDs (Connect ‘Signal’ to the Anode or long lead and ‘GND’ to Cathode or short lead)

You can also use the worksheets that can be downloaded for the CamJam EduKit #3. These are an excellent way to test and learn more about the functions provided by the PiZ-Moto+ and we highly recommend the EduKit3 as a kit for your Raspberry Pi if you want to get a kick-start in understanding how to interface motors & sensors to your Raspberry Pi.

7) There are examples and a Python Package for the PiZ-Moto on GitHub. To install the package and examples:
a. Log on to the pi as usual, opening a terminal window if you’re in the Pixel GUI and navigate to the /users/pi/home folder;
b. Clone the PiZ-Moto GitHub folder into piz-moto

git clone https://github.com/astro-designs/piz-moto.git

c. The examples can be found in the examples folder within the piz-moto folder;
d. The piz-moto ‘package’ can be loaded into any Python code running in the home folder using import piz-moto;
8) Connect the battery again and switch it on.
9) Run the Python script [piz-moto_test.py], following the instructions on-screen or over a terminal;

If you encounter any problems, maybe a motor only works one way, one or more of the sensors doesn’t work, one or both LEDs doesn’t work, then double check all soldering, re-flowing any joints that you’re not sure about.

Prerequisites of the example code
If you’re going to use the Bluetooth based “Wii-Mote” controller then you’ll need to install the CWiid module so that Python can talk to the Wiimote.

Install cwiid using
sudo apt-get install python-cwiid

Examples
1) The Python script PiZ-Moto_Wii.py is designed to control a 2-motor wheeled robot with line-following and object avoidance functions. It’s also primarily designed to work with a BlueTooth based “Wiimote” controller.

www.astro-designs.com/downloads/piz-moto/examples/piz-moto_wii.py

2) The Python script PiZ-Moto_ kb.py is designed to control a 2-motor wheeled robot with line-following and object avoidance functions. This version is primarily designed to work with a wireless USB keyboard.

Note: the PiZiMoto_kb.py script isn’t ready yet but we’ll hope to get it ready early July 2016.

www.astro-designs.com/downloads/piz-moto/examples/piz-moto_kb.py

3) The board is designed to be 100% compatible with the CamJam EduKit #3 so the worksheets designed for the EduKit #3, and the sensors that come as part of that kit, will all run on the PiZ-Moto. We highly recommend getting hold of the EduKit #3 if you want to get going playing with motors with the Raspberry Pi.

Frequently Asked Questions

Q) What’s the recommended power supply?
A) It was designed to run from 6V. It can handle more and has been tested at 9V, but only with minimum loading on the 5V supply rail. And it can take less, as little as 5.5V. But the recommended supply is 6V. Four x AA cells make an ideal power supply.
Q) Can it use rechargeable AA cells?
A) Rechargeable AA cells are slightly lower voltage than Alkaline AA cells. Rechargeable AA cells (NiMH) are 1.2V So four cells make 4.8V. This is under the minimum 5.5V supply so these will not work. However, it will work well with five (6.0V) or six (7.2V) NiMH rechargeable AA cells.
Q) Can it support a WiFi dongle on the Raspberry Pi?
A) Yes. They can be a little power-hungry and can cause the 5V regulator to run quite hot but it can work. We would recommend that you run off a power supply voltage of no more that 6V when using WiFi to help keep the temperature of the 5V regulator down. We also recommend screwing the 5V regulator to the PCB using an M3 screw. No need to insulate the screw as the tab of the regulator is already electrically connected to the copper pad under the regulator. Add a little heatsink compound if you have some to improve the thermal connection to the PCB. The PCB will then help sink some of the heat generated in the regulator.
Q) Will it work with the Raspberry Pi A, B, B+, 2 or 3?
A) It’s designed for the Pi Zero, because the Pi Zero has a lower power consumption than other versions of the Raspberry Pi. It’s not designed to supply much current on the 5V power rail, that’s how we get away with using an easy to assemble & low-cost 5V regulator. However, depending on what you connect to the 5V supply, yes it can possibly work with other versions of the Raspberry Pi. The 5V regulator is rated to supply up to 1A so the total current draw on the 5V supply, including the Pi, any USB dongles and anything loading the 5V pins on the Pi’s GPIO connector must be less than 1A. However, since the 5V regulator is a ‘linear regulator’ it’s not as efficient as a ‘switching regulator’ and it can get quite hot, especially when the supply voltage is greater than 6V. If you’re going to load up the 5V supply rail with current-thirsty USB dongles (e.g. WiFi) or plug heavy loads into the GPIO connector then you should try to keep the supply voltage to around 6V. Also, keep an eye on the temperature of the regulator. If it gets hot then you probably need a heatsink to help keep the temperature down or you need to reduce the load on the 5V supply.
Q) How much can I connect to the 5V supply.
A) Please see the previous answers related to WiFi dongles and using it with the Raspberry Pi 2 or 3.
Q) Can I power the Raspberry Pi from the 5V USB power or data connectors?
A) It is not recommended but it does work. If you’re connecting a USB power supply to the Pi Zero while it’s plugged into the PiZ-Moto, disconnect the power supply to the PiZ-Moto.
Q) Can I use a separate power supply for the motors and a separate USB power supply for the Raspberry Pi?
A) If you want to do this, it’s advised to not fit the Linear Regulator. If the Linear Regulator is not fitted then it is perfectly safe to use a separate power supply for the motors using the Power Connector on the PiZ-Moto+ and power the Raspberry Pi from the USB power connector on the Raspberry Pi as normal. You can then power the motors at up to 36V but do not connect a servo to the servo connector if using a supply larger than 7.2V as you will very likely destroy the servo.
Q) Can I run the camera on the Pi Zero when it’s powered from the PiZ-Moto?
A) We’ve not tested this at the time of writing this document but we believe this is probably ok. The current consumption of the camera is around 200 – 400mA (TBC) which should be fine. We’d recommend using a power supply voltage of no more than a 6V supply for this. If you try using the camera or any extra load on the 5V supply, keep an eye on the temperature of the regulator.
Q) Which motor terminal is for the left motor & which terminal is for the right motor?
A) It really depends on how your software is written but if your using our example code or the code from the EduKit #3 then J3 should connect to the right motor, J4 should connect to the left motor.
Q) Which way round should I connect the red & black leads from the motors?
A) This really depends on how your motors are wired. The motors from the CamJam EduKit 3 seem to work fine when connected as described in the picture in the earlier section on Connecting The

Motors. If you find the motors run the wrong way, simply swap the red / black wires to the motor that’s running the wrong way.

Q) What kind of motors can I use?
A) Small, low-current DC brushed motors. Here are a few examples:

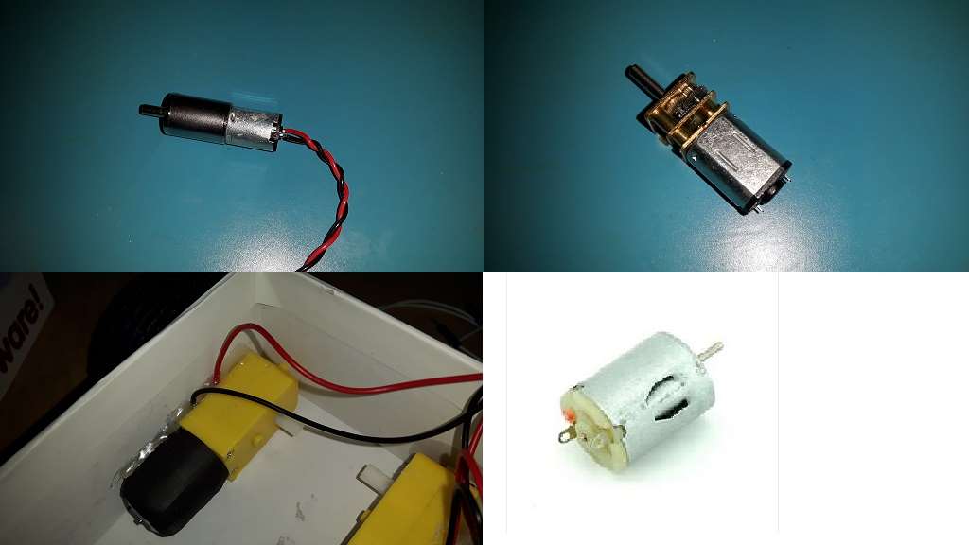
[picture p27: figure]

Have fun with your Astro Designs PiZ-Moto+

@AstroDesignsLtd

www.astro-designs.com

Acknowledgements

“Raspberry Pi” is a trademark of The Raspberry Pi Foundation.

The “CamJam EduKit #3” was created by the organisers of the Cambridge Raspberry Jam and is distributed by ThePiHut. Find them at: https://thepihut.com/

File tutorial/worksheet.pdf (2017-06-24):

# Motor Control Tutorial Cotswold Raspberry Jam, 24th June, 2017

A tutorial by Mark Cantrill @AstroDesignsLtd

In this tutorial we’re going to look at what we need to do control a motor with the Raspberry PI, how a motor driver works and we’re going to look at using the PiZ-Moto motor driver for the Raspberry Pi to control two motors. We’ll also look at how we might program a small two-wheeled robot.

This worksheet focuses on the use of the PiZ-Moto motor driver board.

1) Connecting the motor(s)

There are two connectors on the PiZ-Moto board, one is for Motor1 and one is for Motor2. The connectors are screw terminals, simply push the wires of the motor into the terminals and do up the screw in the top of the connector ‘finger-tight’. The connector on the left is for Motor1, the connector on the right is for Motor2.

For this tutorial we’re only using one motor but the second motor connector has a couple of LEDs wired into it to show changes in direction and also changes in motor speed through the brightness of the LED. The LEDs are connector to Motor1 connector, the motor is connected to the Motor2 connector.

2) Connecting the Power Supply

The PiZ-Moto is designed to run off a 6V 4-cell AA battery pack. We’ve included one of these and the wires to connect it with the PiZ-Moto in this tutorial. But for the purpose of this tutorial, to save us from buying lots of batteries, we’ve temporarily connected a wire from the Raspberry Pi’s 5V pin to the VIN (+) connection on the PiZ-Moto which enables us to run this tutorial off of a 5V USB power supply plugged into the Raspberry Pi.

This is ok for this tutorial where we’re only using one small motor like this but we highly recommend that you cut this wire off and power the PiZ-Moto from the battery pack.

PLEASE remove the wire before connecting a battery pack as it will permanently damage your Raspberry Pi. The Raspberry Pi needs 5V, connecting a 6V battery to it will damage the Raspberry Pi.

Also please note that when powering the PiZ-Moto from the battery pack, the 5V regulator on the PiZ-Moto will provide the Raspberry Pi with 5V. There is no need to connect a USB power supply to your Raspberry Pi when using the PiZ-Moto, in fact if you did do this then you could damage the power supply.

3) Writing the software (using Python)
i) Import the PiZ-Moto package

import piz_moto

ii) | Understand the functions that you’ll need to use
| piz_moto.Motor1(speed,duration)
| Where, speed is: -100 to +100
| Max speed = 100 or -100
| Use positive speeds for forwards (e.g. 100)
| Use negative speeds for backwards (e.g. -100)
| Use smaller numbers to slow the motor down (e.g. 50 for half speed)
| Use 0 to make the motor stop
| And duration is: the length of time in seconds that you want the motor to run
for.
| e.g. 20 will make the motor run for 20 seconds.
| e.g. 0.5 will make the motor run for half a second
| If time = 0 then the motor will run until you tell it to stop by setting the speed to 0.
iii) | Now let’s make the motors do something… Motor1 forwards for 10 seconds
| piz-moto.Motor1(100, 10)
| Motor2 backwards for 10 seconds
| piz_moto.Motor2(-100,10)
4) Task 1: Write a program to control a robot…
Pretend you have two motors on a two wheeled robot. Write a program to make it go forwards for 5 seconds then backwards for 5 seconds.
5) Task 2: Make your robot turn…
Add a routine to your last program so that your robot turns left (or right) for 1 second before it changes direction from forwards to backwards.
6) Task 3: Make your robot accelerate…
Modify your program so that instead of going forwards at full speed, it increases the speed over a period of 5 seconds.

Other useful information on the PiZ-Moto

Full instructions for the assembly of the PiZ-Moto (if you have a kit) are on github, together with some examples. We’ve already cloned the github piz_moto repository onto the SDCard supplied with the tutorial so you’re ready to go! But please keep an eye out for updates.

How to clone piz-moto repository onto your Raspberry Pi if it’s not there. Or if you just want to put a fresh copy in a new folder.

To clone piz_moto into your home folder (/home/pi) run the following command. This will create a folder called piz-moto that contains the simple piz_moto package, instructions & examples.

cd /home/pi

git clone https://github.com/astro-designs/piz-moto.git

If you simply want to check for updates, just navigate into the piz-moto folder and run git pull:

cd /home/pi/piz-moto

git pull

Please note that for the purpose of running this tutorial, the SDCard has been prepared with the piz_moto files cloned to the following folder. You can continue to use it in this folder and run the git pull function to update the files as long as you are inside this folder:

/home/pi/python/motors

The instructions found inside the piz-moto folder are worth a read as they explain all about the PiZ-Moto. For one thing, it’s not just a motor driver… The PiZ-Moto includes simple interfaces to allow you to connect an ultrasonic range sensor to and infra-red photo-sensor. It also includes a 5V regulator that you can use to power the Raspberry Pi. Plus there are two general purpose outputs that include an on-board series 100-ohm resistor so you can connect a couple of LEDs direct to these pins.

Have fun with your PiZ-Moto motor driver board for the Raspberry Pi!

Worksheet Rev 2

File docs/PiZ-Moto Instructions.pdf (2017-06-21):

# PiZ-Moto

(Pronounced “Pie-Zee Moto”)

## Assembly Instructions (1.5)

Produced for the Cotswold Raspberry Jam (@CotswoldJam)

Latest instructions available at:

www.astro-designs.com/downloads/piz-moto/instructions/PiZ-Moto_Instructions.pdf

Contents

In your kit, you should find:

1) PiZ-Moto PCB (x1)
2) 100 Ohm Resistors (x3)
3) 1.8k Ohm Resistors (x2)
4) 3.3k Ohm Resistors (x2)
5) BA50BCT (or similar) Low-dropout Linear Regulator (x1)
6) L293DNE Quad Half-Bridge Driver I.C. (x1)
7) I.C. Socket (x1)
8) 2-way Screw Terminal (x3)
9) 3mm single-colour LED (x1)
10) 20-way Pin Header (x1)
11) 22uF 16V Aluminium Electrolytic Capacitors (x2)
12) 40-way Socket (x1)

Introduction

Firstly, thank-you for choosing the PiZ-Moto. The PiZ-Moto kit is based around the L293DNE quad half-bridge driver which can be used to control up to two motors in both directions. The L293DNE was chosen because it’s pretty much the only driver you can find like this that’s not surface-mount making it ideal for a kit like this. We wanted to make this motor driver a little different from others, after all there are quite a few available so what makes this one different? Firstly, it includes a built-in power supply so that the power source used to power the motors can also be used to power the Raspberry Pi Zero. Secondly, it includes interfaces for a photo-reflecting sensor, a proximity sensor and a couple of LEDs. For the power supply we chose a low drop-out linear regulator because they are cheap, easily assembled from a kit like this and because they are low drop-out, it means that the motor supply voltage only needs to be 0.3V greater than the 5V supply needed by the Raspberry Pi. So a 4-cell AA battery pack which produces 6V, makes an ideal power source for this motor driver kit. With the motor driver, regulator, and the extra interfaces on the board, you can build a intelligent line-following, object avoiding robot using with just a single add-on board for the Raspberry Pi Zero.

Tools Required

1) A reasonably decent soldering iron
2) Solder wire
3) A pair of snips
4) A pair of snipe-nosed Pliers

Assembly Instructions

Right, let’s get stuck in…

1) It’s always best to start with the smallest components so firstly we’ll fit the resistors, then gradually move through the taller components. There are three different values of resistors used so let’s fit these in turn.
a. Firstly, fit the three x 100 ohm resistors.
These are colour-coded BROWN-BLACK-BROWN [GOLD]

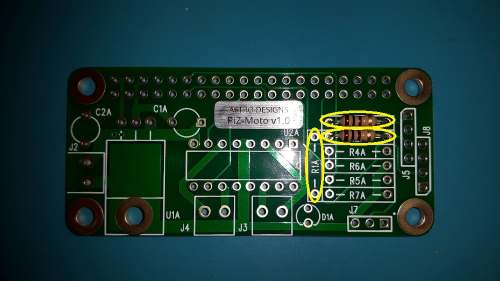
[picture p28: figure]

Note – Yes, I did actually forget to fit one of these before taking the picture. R1A must also be fitted (100 ohm) – if you don’t fit it then the LED won’t work.

Oh and just to make it look nice and neat, you might want to arrange the gold bands at the same end, or is that just me being finicky?

b. Next, fit the two 1.8k ohm resistors.
These are colour-coded BROWN-GREY-RED [GOLD]

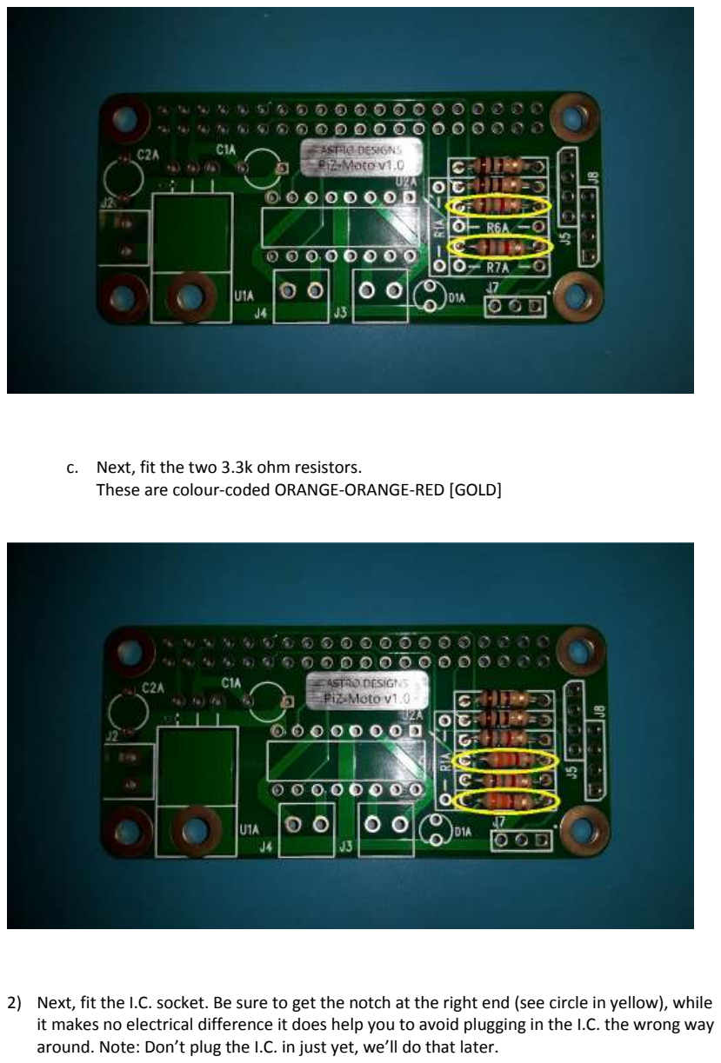
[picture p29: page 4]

c. Next, fit the two 3.3k ohm resistors.
These are colour-coded ORANGE-ORANGE-RED [GOLD]
2) Next, fit the I.C. socket. Be sure to get the notch at the right end (see circle in yellow), while it makes no electrical difference it does help you to avoid plugging in the I.C. the wrong way around. Note: Don’t plug the I.C. in just yet, we’ll do that later.

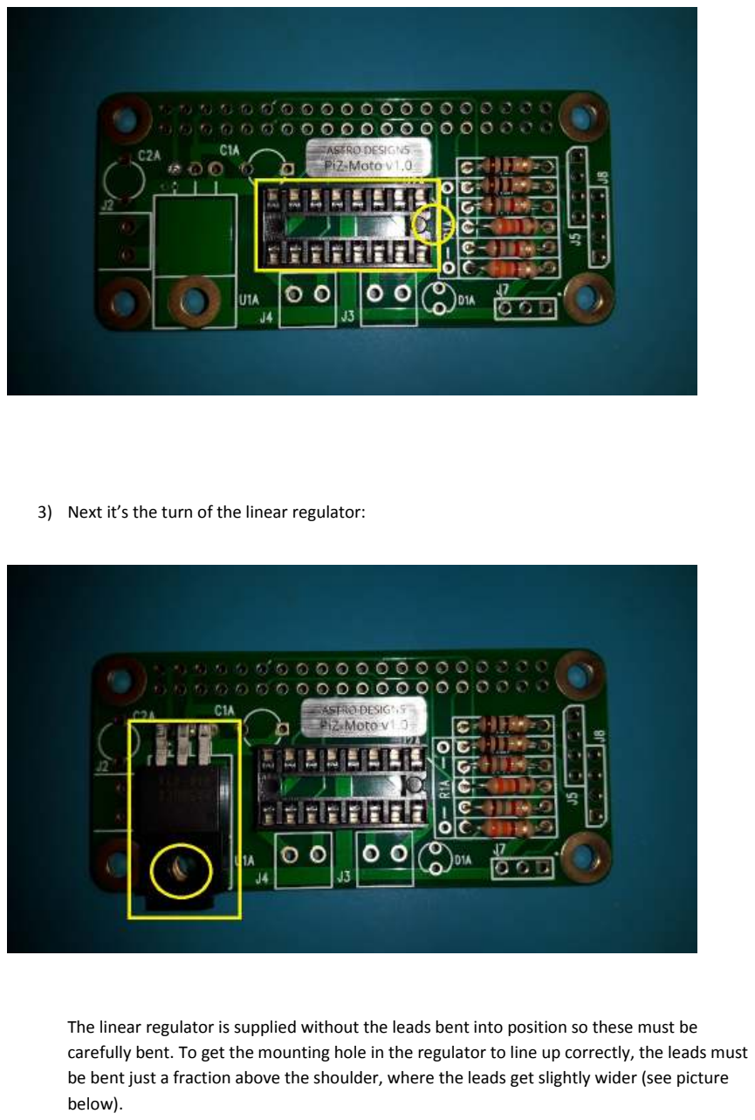
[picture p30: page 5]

3) Next it’s the turn of the linear regulator:

The linear regulator is supplied without the leads bent into position so these must be carefully bent. To get the mounting hole in the regulator to line up correctly, the leads must be bent just a fraction above the shoulder, where the leads get slightly wider (see picture below).

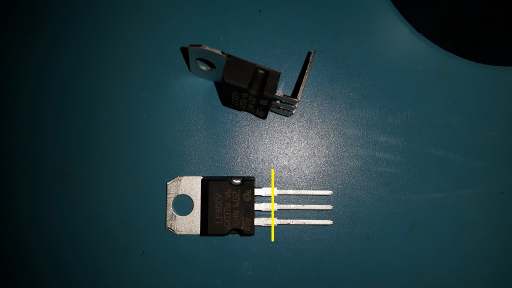
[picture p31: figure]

4) Fit the LED:
a. Ensure that the LED is fitted the correct way around. The ‘cathode’ which is indicated by the shorter lead, must go at the bottom of the board. The circle outline for the LED has a flat section to mark the ‘cathode’, also marked with the yellow arrow in the picture below.

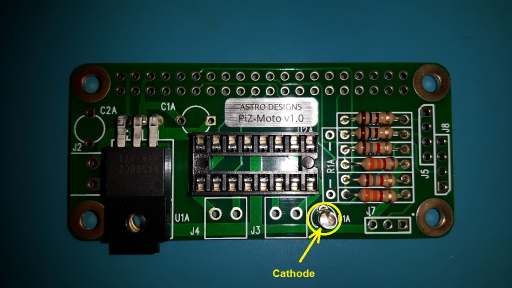
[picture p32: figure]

5) Next, fit the three 2-way screw-terminals:
a. Try to keep them flat against the surface of the board as you solder them. It also helps when connecting the motor leads if the holes in the side for connecting the wires face outwards (yes, I did put one in the wrong way around once…);

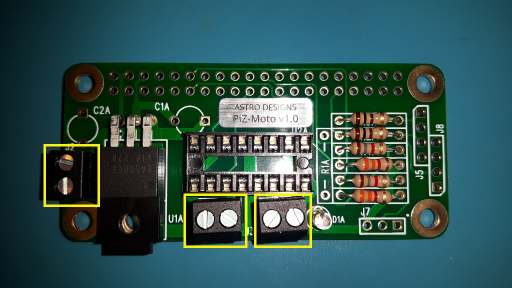
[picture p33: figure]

6) Next, fit the three pin-headers. Two of these are four-pin, the third is three-pin. These need to be carefully broken off the 20-pin strip provided. This will leave a few spare which are not needed for this project.

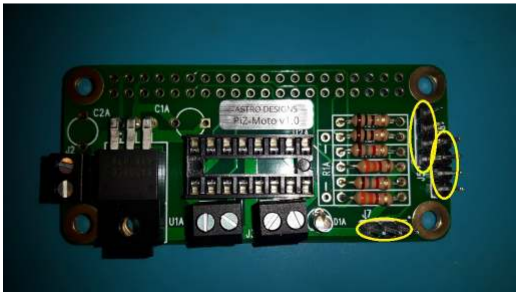
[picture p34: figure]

7) Next, fit the two large capacitors. Firstly, these need to have the pins ‘formed’ slightly to match the separation of the holes on the board. The pins should be separated by about the same amount as the diameter of the capacitor. See the additional picture below illustrating how they should look. Secondly, it’s important to note that these are polarised capacitors so they MUST be fitted the correct way around. The negative terminal is marked on the capacitor with a stripe and “-“ symbols. The arrows on the picture below point to where the negative terminal should go. One of the terminals for the capacitor shape on the PCB has a square pad, this corresponds to the positive lead on the capacitor.

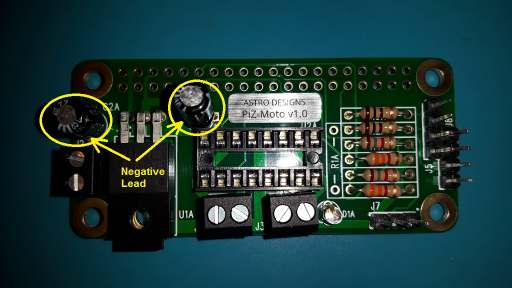
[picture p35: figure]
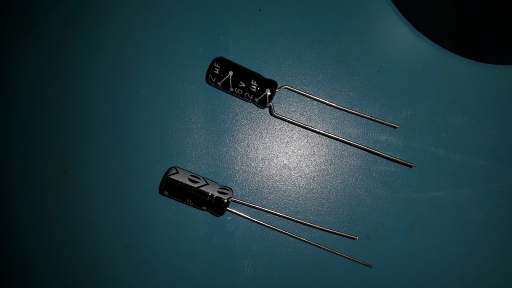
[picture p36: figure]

8) Next, fit the 40-way socket. Note this needs to be assembled onto the opposite side of the board with the pins coming through to the top side.

It’s best to solder just two pins in opposite corners to start with, then while pressing the connector into the board, re-melt the solder on those two pins just to ensure the connector

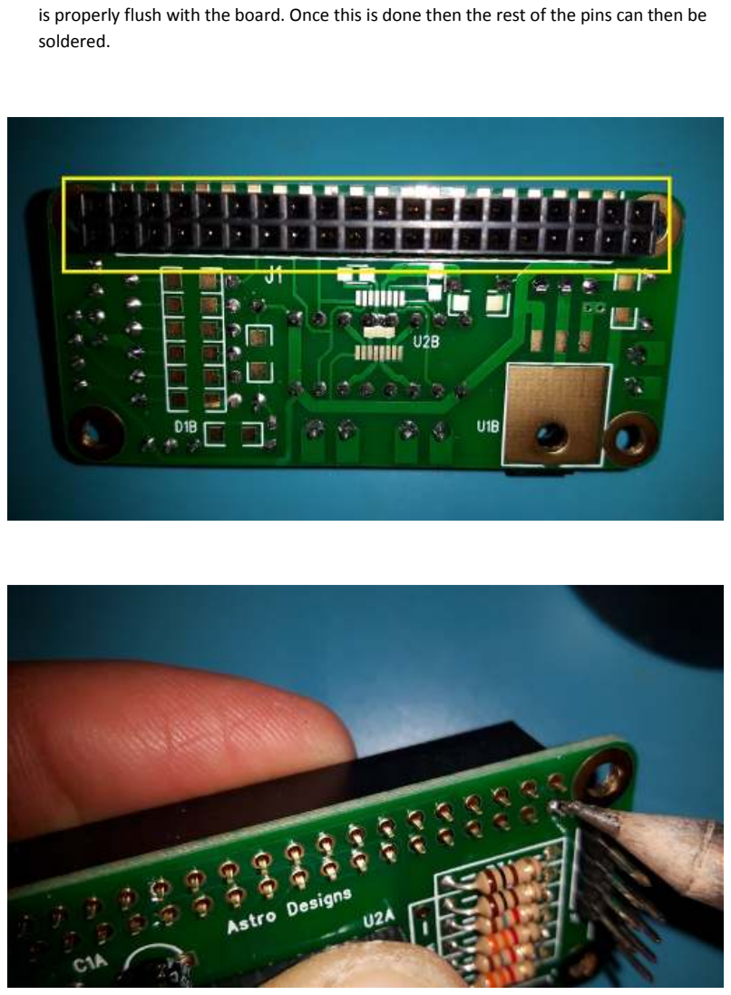
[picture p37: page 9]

is properly flush with the board. Once this is done then the rest of the pins can then be soldered.

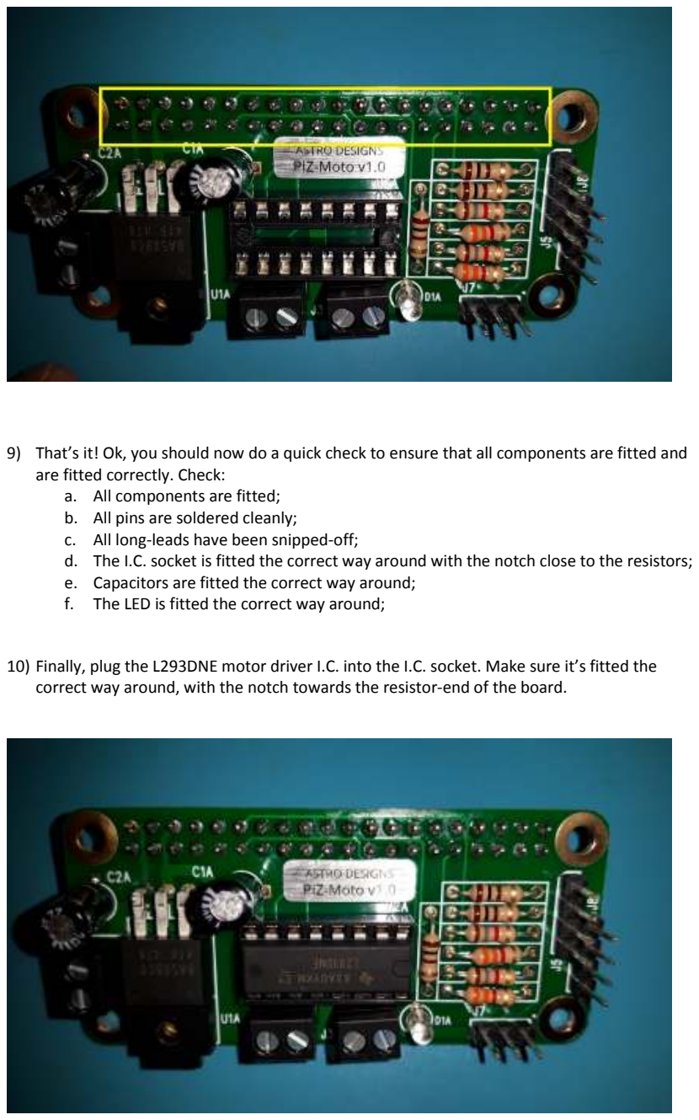
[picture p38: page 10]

9) That’s it! Ok, you should now do a quick check to ensure that all components are fitted and are fitted correctly. Check:
a. All components are fitted;
b. All pins are soldered cleanly;
c. All long-leads have been snipped-off;
d. The I.C. socket is fitted the correct way around with the notch close to the resistors;
e. Capacitors are fitted the correct way around;
f. The LED is fitted the correct way around;
10) Finally, plug the L293DNE motor driver I.C. into the I.C. socket. Make sure it’s fitted the correct way around, with the notch towards the resistor-end of the board.

Connecting the motors

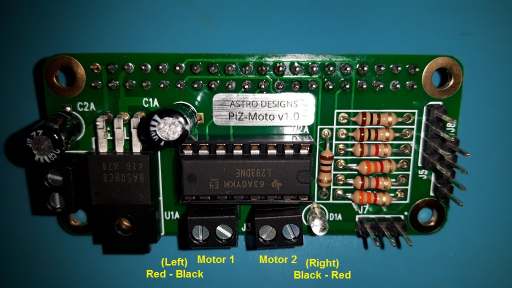
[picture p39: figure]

Each pair of screw terminals above connects to a single motor. In theory you could connect two motors in parallel, with two motors on a single screw terminal but start with one motor per screw terminal pair. The motor driver is rated to 600mA per motor.

Connecting the battery:

It’s important to get the polarity correct when connecting the battery. Getting this wrong could damage the board. The ground / black / 0V wire from the battery should connect to the battery screw terminal that’s closest to the corner of the board (marked in yellow as “-“ in the picture below). The positive / red wire from the battery should connect to the other screw terminal, marked below in yellow as “+”.

It’s best to have a switch in line with your battery so that it’s easy to turn things off. Make sure the switch is off when connecting the battery to the board.

Important note: The PiZ-Moto is designed to be powered through the screw-terminal power connector. The PiZ-Moto uses an on-board 5V regulator to provide a 5V regulated power supply to the Raspberry Pi Zero through the Pi’s +5V & GND pins on the Pi’s GPIO connector. Please do not power the Pi through the Pi’s USB power connector while connected to the PiZ-Moto. While this is unlikely to result in any damage, you will not be able to provide power to the motors using the Pi’s USB power connector so it recommended that you don’t use that connector when using the PiZ-Moto.

It’s designed to run off four “AA” cells which would provide approximately 6V. But it will work on as little as 5.3V. The recommended upper limit is 6.5V although it will tolerate more. How much it can tolerate comes down to how much current is needed by the Pi Zero. If you connect a USB WiFi dongle or a camera then I wouldn’t recommend anything more than 6V. Also check the temperature of the regulator (U1A) as this gets hot as the Pi Zero draws more current.

It’s really best suited to minimal applications where the loading on the Pi Zero is very little. A Bluetooth dongle or Wireless Keyboard Dongle consumes very little power so these are ideal.

One final note on the battery side of things, you don’t need to (& shouldn’t) power the Pi Zero separately. The Pi Zero is powered from the regulator on the PiZ-Moto.

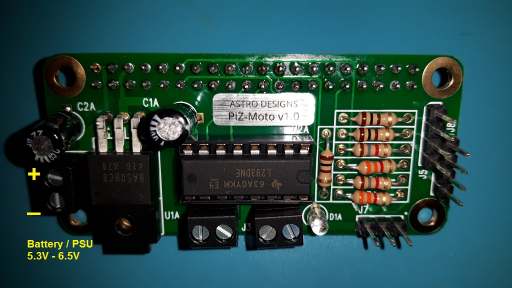
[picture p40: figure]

Connecting the Photo Sensor

The Photo Sensor Header is designed to connect directly to a photo-reflector / line sensor like the one found in the CamJam EduKit #3. Simply connect the three pins on the PiZ-Moto Photo Sensor Header to the three pins on the photo-reflector / line sensor, making sure you get the pins connected to the right terminals on the photo-reflector board and you’ll be ready to test.

The signal connection on the PiZ-Moto Photo Sensor Header can also be used as a general-purpose 5V input and is connected to the Pi Zero’s GPIO-25.

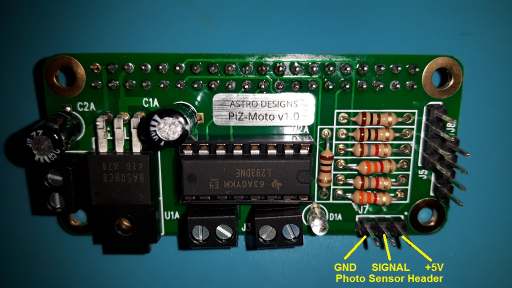
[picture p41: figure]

Connecting the Range Sensor

The Range Sensor header is designed to connect directly to an SR-04 range sensor, as found in the CamJam EduKit #3. The SR-04 is also available separately from several suppliers. Simply connect the four pins on the PiZ-Moto Range Sensor Header to the four pins on the SR-04, making sure you get the pins connected to the right terminals on the SR-04 and you’ll be ready to test.

he Echo connection on the PiZ-Moto Photo Sensor Header can also be used as a general-purpose 5V input and is connected to the Pi Zero’s GPIO-18 via a 5V to 3.3V level shifting network. The Trig connection can be used as a general-purpose 3.3V input or output and is connected directly to the Pi Zero’s GPIO-17

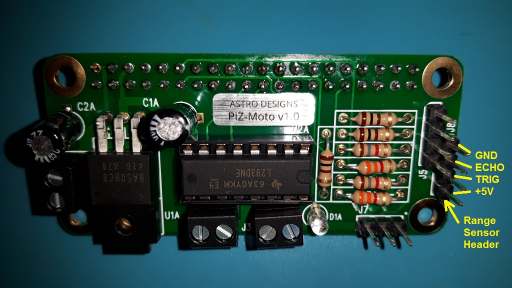
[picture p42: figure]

Connecting the LEDs

The LED header is really a couple of general purpose I/O pins, each provided paired with it’s own ‘GND’. The two LED pins have a 100 ohm resistor in series with it’s connection the header on the Pi Zero. This both protects the I/O on the Pi Zero as well as allowing an LED to be connected directly across the two pins. No external resistor is necessary. In our examples here, we just connect a couple of LEDs directly but you could use these pins as inputs or outputs.

The LED1+ connection on the LED Header is connected to the Pi Zero’s GPIO-5 via a 100 ohm resistor. The LED2+ connection is connected to the Pi Zero’s GPIO-6 via a 100 ohm resistor.

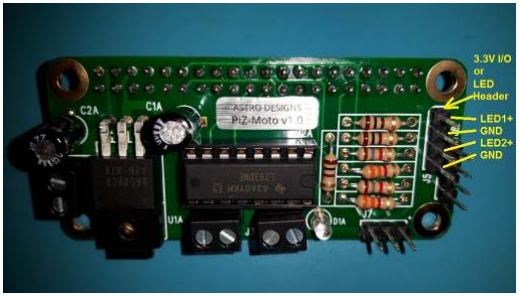
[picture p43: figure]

That’s it, you’re now ready to run some quick tests and start using your PiZ-Moto

Testing

1) Firstly, connect the battery and switch it on (if there’s a switch).
2) Check that the LED comes on;
3) Measure the voltage on the “+5V” terminals of the 40-way socket. These should be very close to 5.0V;
4) Disconnect the battery and check that the LED goes off;
5) Connect the PiZ-Moto to a Raspberry Pi Zero. Take care to ensure that the connector lines up correctly and is not offset by (say) one pin. (Yes, I’ve done that too and now have a PiZero that’s minus a GPIO output )
6) The Python script PiZ-Moto_test.py is the best way to test the board. If you connect the battery, motors, LEDs, line sensor & proximity sensor and run the script, it’ll quickly exercise all functions on the PiZ-Moto allowing you to check it all works. You’ll need a Pi Zero with HDMI display & USB keyboard connected.
a. Plug a small DC brushed motor into each motor terminal;
b. Connect the 3-pin photo sensor header to a photo-reflector / line detector;
c. Connect the 4-pin range sensor header to a SR-04 ultrasonic range sensor;
d. Connect the 4-pin LED / 3.3V I/O header to a couple of LEDs
7) Connect the battery again and switch it on.
8) Run the Python script [piz-moto_test.py], following the instructions on-screen or over a terminal;

www.astro-designs.com/downloads/piz-moto/examples/piz-moto_test.py

If you encounter any problems, maybe a motor only works one way, one or more of the sensors doesn’t work, one or both LEDs doesn’t work, then double check all soldering, re-flowing any joints that you’re not sure about.

Prerequisites of the example code
If you’re going to use the Bluetooth based “Wii-Mote” controller then you’ll need to install the CWiid module so that Python can talk to the Wiimote.

Install cwiid using
sudo apt-get install python-cwiid

Examples
1) The Python script PiZ-Moto_Wii.py is designed to control a 2-motor wheeled robot with line-following and object avoidance functions. It’s also primarily designed to work with a BlueTooth based “Wiimote” controller.

www.astro-designs.com/downloads/piz-moto/examples/piz-moto_wii.py

2) The Python script PiZ-Moto_ kb.py is designed to control a 2-motor wheeled robot with line-following and object avoidance functions. This version is primarily designed to work with a wireless USB keyboard.

Note: the PiZiMoto_kb.py script isn’t ready yet but we’ll hope to get it ready early July 2016.

www.astro-designs.com/downloads/piz-moto/examples/piz-moto_kb.py

3) The board is designed to be 100% compatible with the CamJam EduKit #3 so the worksheets designed for the EduKit #3, and the sensors that come as part of that kit, will all run on the PiZ-Moto. We highly recommend getting hold of the EduKit #3 if you want to get going playing with motors with the Raspberry Pi.

The Alternative & Adventurous Kit, Possibly…

You may have noticed that there are some surface mount pads on the bottom side of the board. Why are these there? Well we thought we’d do something slightly different to other kits and offer the option of a surface mount kit for those of you feeling a little more adventurous with your soldering iron and who might want to venture into the world of surface mount technology. The majority of the surface mount components designed into this board are relatively easy to fit, the surface mount motor driver on this version on the other hand, isn’t so easy and really needs a finetipped iron, microscope and some extra-fine solder. A steady hand helps too. So we may change that one. But by one way or another we’ll hope to offer a surface mount kit soon.

Frequently Asked Questions

Q) What’s the recommended power supply?
A) It was designed to run from 6V. It can handle more and has been tested at 9V, but only with minimum loading on the 5V supply rail. And it can take less, as little as 5.3V. But the recommended supply is 6V. 4 x AA cells are an ideal supply.
Q) Can it support a WiFi dongle on the Raspberry Pi?
A) Yes. They can be a little power-hungry and can cause the 5V regulator to run quite hot but it can work. We would recommend that you run off a power supply voltage of no more that 6V when using WiFi to help keep the temperature of the 5V regulator down.
Q) Will it work with the Raspberry Pi A, B, B+, 2 or 3?
A) It’s designed for the Pi Zero, because the Pi Zero has a lower power consumption than other versions of the Raspberry Pi. It’s not designed to supply much current on the 5V power rail, that’s how we get away with using an easy to assemble & low-cost 5V regulator. However, depending on what you connect to the 5V supply, yes it can possibly work with other versions of the Raspberry Pi. The 5V regulator is rated to supply up to 1A so the total current draw on the 5V supply, including the Pi, any USB dongles and anything loading the 5V pins on the Pi’s GPIO connector must be less than

1A. However, since the 5V regulator is a ‘linear regulator’ it’s not as efficient as a ‘switching regulator’ and it can get quite hot, especially when the supply voltage is greater than 6V. If you’re going to load up the 5V supply rail with current-thirsty USB dongles (e.g. WiFi) or plug heavy loads into the GPIO connector then you should try to keep the supply voltage to around 6V. Also, keep an eye on the temperature of the regulator. If it gets hot then you probably need a heatsink to help keep the temperature down or you need to reduce the load on the 5V supply.

Q) How much can I connect to the 5V supply.
A) Please see the previous answers.
Q) Can I power the Raspberry Pi from the 5V USB power or data connectors?
A) It is not recommended but it does work. If you’re connecting a USB power supply to the Pi Zero while it’s plugged into the PiZ-Moto, disconnect the power supply to the PiZ-Moto.
Q) Can I run the camera on the Pi Zero when it’s powered from the PiZ-Moto?
A) We’ve not tested this at the time of writing this document but we believe this is probably ok. The current consumption of the camera is around 200 – 400mA (TBC) which should be fine. We’d recommend using a power supply voltage of no more than a 6V supply for this. If you try using the camera, or any extra load on the 5V supply, keep an eye on the temperature of the regulator.
Q) Which motor terminal is for the left motor & which terminal is for the right motor?
A) J3 should connect to the right motor, J4 should connect to the left motor.
Q) Which way round should I connect the red & black leads from the motors?
A) This really depends on how your motors are wired. The motors from the CamJam EduKit 3 seem to work fine when connected as described in the picture in the earlier section on Connecting The Motors.
Q) What kind of motors can I use?
A) Small, low-current DC brushed motors. Here’s a few examples:

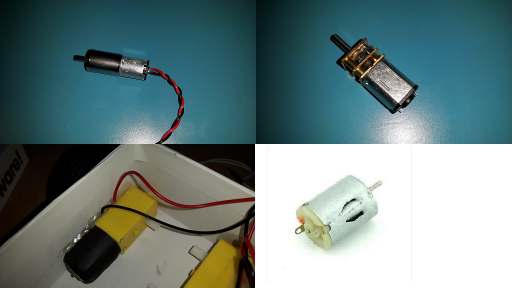
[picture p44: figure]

Have fun with your Astro Designs PiZ-Moto

@AstroDesignsLtd

www.astro-designs.com

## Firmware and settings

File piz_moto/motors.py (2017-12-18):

#!/usr/bin/env python2.7
# PiZ-Moto Motor Control Functions

# First some basic motor control functions to control each motor separately
# SpeedAndDirection can be a number between +100 & -100
# +100 or any value greater than zero spins the motor forwards
# -100 or any value less than zero spins the motor backwards
# 100 or -100 (100% duty-cycle) spins the motor at full speed
# 50 or -50 (50% duty-cycle) spins the motor at half speed

#Motor 1
def Motor1(SpeedAndDirection, pwmMotorAForwards, pwmMotorABackwards):

	if SpeedAndDirection > 100:
		SpeedAndDirection = 100
		
	if SpeedAndDirection < -100:
		SpeedAndDirection = -100
		
	if(SpeedAndDirection < 0):
		SpeedAndDirection = SpeedAndDirection * -1
		pwmMotorAForwards.ChangeDutyCycle(0)
		pwmMotorABackwards.ChangeDutyCycle(SpeedAndDirection)
	else: # Forwards...
		pwmMotorAForwards.ChangeDutyCycle(SpeedAndDirection)
		pwmMotorABackwards.ChangeDutyCycle(0)
	
#Motor 2
def Motor2(SpeedAndDirection, pwmMotorBForwards, pwmMotorBBackwards):

	if SpeedAndDirection > 100:
		SpeedAndDirection = 100
		
	if SpeedAndDirection < -100:
		SpeedAndDirection = -100
		
	if(SpeedAndDirection < 0): # Backwards...
		SpeedAndDirection = SpeedAndDirection * -1
		pwmMotorBForwards.ChangeDutyCycle(0)
		pwmMotorBBackwards.ChangeDutyCycle(SpeedAndDirection)
	else: # Forwards...
		pwmMotorBForwards.ChangeDutyCycle(SpeedAndDirection)
		pwmMotorBBackwards.ChangeDutyCycle(0)



# Next, some functions to control both motors for driving a two motor, two-wheeled robot...
		
# Function to turn all motors off
def Stop(pwmMotorAForwards, pwmMotorABackwards, pwmMotorBForwards, pwmMotorBBackwards):

	#print("Stop")
	pwmMotorAForwards.ChangeDutyCycle(0)
	pwmMotorABackwards.ChangeDutyCycle(0)
	pwmMotorBForwards.ChangeDutyCycle(0)
	pwmMotorBBackwards.ChangeDutyCycle(0)
	
# Turn both motors backwards
def Backwards(DCA, DCB, pwmMotorAForwards, pwmMotorABackwards, pwmMotorBForwards, pwmMotorBBackwards, Speed):

	#print("Backwards")
	pwmMotorAForwards.ChangeDutyCycle(0)
	pwmMotorABackwards.ChangeDutyCycle(DCA * Speed)
	pwmMotorBBackwards.ChangeDutyCycle(0)
	pwmMotorBForwards.ChangeDutyCycle(DCB * Speed)

# Turn both motors forwards
def Forwards(DCA, DCB, pwmMotorAForwards, pwmMotorABackwards, pwmMotorBForwards, pwmMotorBBackwards, Speed):
	
	#print("Forwards")
	pwmMotorAForwards.ChangeDutyCycle(DCA * Speed)
	pwmMotorABackwards.ChangeDutyCycle(0)
	pwmMotorBBackwards.ChangeDutyCycle(DCB * Speed)
	pwmMotorBForwards.ChangeDutyCycle(0)
	
# Spin Right
def SpinRight(DCA, DCB, pwmMotorAForwards, pwmMotorABackwards, pwmMotorBForwards, pwmMotorBBackwards, Speed):
	
	#print("Spin Right")
	pwmMotorAForwards.ChangeDutyCycle(DCA * Speed)
	pwmMotorABackwards.ChangeDutyCycle(0)
	pwmMotorBBackwards.ChangeDutyCycle(0)
	pwmMotorBForwards.ChangeDutyCycle(DCB * Speed)
	
def BLeft(DCA, DCB, pwmMotorAForwards, pwmMotorABackwards, pwmMotorBForwards, pwmMotorBBackwards, Speed):
	
	#print("Back Left")
	pwmMotorAForwards.ChangeDutyCycle(DCA * Speed * 0.5)
	pwmMotorABackwards.ChangeDutyCycle(0)
	pwmMotorBForwards.ChangeDutyCycle(DCB * Speed)
	pwmMotorBBackwards.ChangeDutyCycle(0)
	
def FLeft(DCA, DCB, pwmMotorAForwards, pwmMotorABackwards, pwmMotorBForwards, pwmMotorBBackwards, Speed):
	
	#print("Forwards Left")
	pwmMotorABackwards.ChangeDutyCycle(0)
	pwmMotorAForwards.ChangeDutyCycle(DCA * Speed * 0.5)
	pwmMotorBForwards.ChangeDutyCycle(0)
	pwmMotorBBackwards.ChangeDutyCycle(DCB * Speed)
	
# Spin left
def SpinLeft(DCA, DCB, pwmMotorAForwards, pwmMotorABackwards, pwmMotorBForwards, pwmMotorBBackwards, Speed):
	
	#print("Spin Left")
	pwmMotorAForwards.ChangeDutyCycle(0)
	pwmMotorABackwards.ChangeDutyCycle(DCA * Speed)
	pwmMotorBBackwards.ChangeDutyCycle(DCB * Speed)
	pwmMotorBForwards.ChangeDutyCycle(0)
	
def BRight(DCA, DCB, pwmMotorAForwards, pwmMotorABackwards, pwmMotorBForwards, pwmMotorBBackwards, Speed):
	
	#print("Back Right")
	pwmMotorABackwards.ChangeDutyCycle(DCA * Speed)
	pwmMotorAForwards.ChangeDutyCycle(0)
	pwmMotorBForwards.ChangeDutyCycle(DCB * Speed * 0.5)
	pwmMotorBBackwards.ChangeDutyCycle(0)
	
def FRight(DCA, DCB, pwmMotorAForwards, pwmMotorABackwards, pwmMotorBForwards, pwmMotorBBackwards, Speed):
	
	#print("Forwards Right")
	pwmMotorABackwards.ChangeDutyCycle(0)
	pwmMotorAForwards.ChangeDutyCycle(DCA * Speed)
	pwmMotorBForwards.ChangeDutyCycle(0)
	pwmMotorBBackwards.ChangeDutyCycle(DCB * Speed * 0.5)

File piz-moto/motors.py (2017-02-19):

#!/usr/bin/env python2.7
# PiZ-Moto Motor Control Functions

import RPi.GPIO as GPIO # Import the GPIO Library
import time

# Set variables for the GPIO motor pins
pinMotorAForwards = 10
pinMotorABackwards = 9
pinMotorBForwards = 7
pinMotorBBackwards = 8

# How many times to turn the pin on and off each second
Frequency = 20

# How long the pin stays on each cycle, as a percent
DutyCycleA = 100
DutyCycleB = 100

# Setting the duty cycle to 0 means the motors will not turn
Stop = 0

# Function to turn all motors off
def Stop():

	#print("Stop")
	pwmMotorAForwards.ChangeDutyCycle(Stop)
	pwmMotorABackwards.ChangeDutyCycle(Stop)
	pwmMotorBForwards.ChangeDutyCycle(Stop)
	pwmMotorBBackwards.ChangeDutyCycle(Stop)
	
# Turn both motors backwards
def Backwards(Speed):

	#print("Backwards")
	pwmMotorAForwards.ChangeDutyCycle(DutyCycleA * Speed)
	pwmMotorABackwards.ChangeDutyCycle(Stop)
	pwmMotorBForwards.ChangeDutyCycle(DutyCycleB * Speed)
	pwmMotorBBackwards.ChangeDutyCycle(Stop)

# Turn both motors forwards
def Forwards(Speed):
	
	#print("Forwards")
	pwmMotorAForwards.ChangeDutyCycle(Stop)
	pwmMotorABackwards.ChangeDutyCycle(DutyCycleA * Speed)
	pwmMotorBForwards.ChangeDutyCycle(Stop)
	pwmMotorBBackwards.ChangeDutyCycle(DutyCycleB * Speed)
	
# Spin Right
def SpinRight(Speed):
	
	#print("Spin Right")
	pwmMotorAForwards.ChangeDutyCycle(Stop)
	pwmMotorABackwards.ChangeDutyCycle(DutyCycleA * Speed)
	pwmMotorBForwards.ChangeDutyCycle(DutyCycleB * Speed)
	pwmMotorBBackwards.ChangeDutyCycle(Stop)
	
def BLeft(Speed):
	
	#print("Back Left")
	pwmMotorAForwards.ChangeDutyCycle(DutyCycleA * Speed * 0.5)
	pwmMotorABackwards.ChangeDutyCycle(Stop)
	pwmMotorBForwards.ChangeDutyCycle(DutyCycleB * Speed)
	pwmMotorBBackwards.ChangeDutyCycle(Stop)
	
def FLeft(Speed):
	
	#print("Forwards Left")
	pwmMotorAForwards.ChangeDutyCycle(Stop)
	pwmMotorABackwards.ChangeDutyCycle(DutyCycleA * Speed * 0.5)
	pwmMotorBForwards.ChangeDutyCycle(Stop)
	pwmMotorBBackwards.ChangeDutyCycle(DutyCycleB * Speed)
	
# Spin left
def SpinLeft(Speed):
	
	#print("Spin Left")
	pwmMotorAForwards.ChangeDutyCycle(DutyCycleA * Speed)
	pwmMotorABackwards.ChangeDutyCycle(Stop)
	pwmMotorBForwards.ChangeDutyCycle(Stop)
	pwmMotorBBackwards.ChangeDutyCycle(DutyCycleB * Speed)
	
def BRight(Speed):
	
	#print("Back Right")
	pwmMotorAForwards.ChangeDutyCycle(DutyCycleA * Speed)
	pwmMotorABackwards.ChangeDutyCycle(Stop)
	pwmMotorBForwards.ChangeDutyCycle(DutyCycleB * Speed * 0.5)
	pwmMotorBBackwards.ChangeDutyCycle(Stop)
	
def FRight(Speed):
	
	#print("Forwards Right")
	pwmMotorAForwards.ChangeDutyCycle(Stop)
	pwmMotorABackwards.ChangeDutyCycle(DutyCycleA * Speed)
	pwmMotorBForwards.ChangeDutyCycle(Stop)
	pwmMotorBBackwards.ChangeDutyCycle(DutyCycleB * Speed * 0.5)

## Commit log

2017-02-27 Adding definitions for line-sensor, range sensor & leds
2017-06-21 Updating piz_moto package with simple functions to control each motor separately.
    Adding tutorial files
    Adding tutorial worksheet
2017-06-21 Adding PiZ-Moto assembly instructions version 1.6
2017-06-22 Adding a delay to the end of the program to allow the motors to stop cleanly
2017-06-23 Corrected error in motors functions where it was calling the wrong function if the duration parameter was specified.
2017-06-24 Correcting the names of the motor ports to Motor1 & Motor2 Correcting the names of the functions, .MotorA becomes .Motor1 & .MotorB becomes .Motor2
2018-02-18 Adding extra files to help with self assembly of a MicroPiNoon fighting robot using the PiZ-Moto motor-driver
    [BallFoot.stl, BalloonHolder.stl, BalloonMast.stl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]
2018-02-18 Adding some rather rudimentary and rapidly typed assembly instructions for assembling a Micro-Pi-Noon 3D printed balloon-popping fighting robot.
2018-03-17 A few extra notes on the 3D printable MicroPiNoon robots
2018-06-23 Updating control interface to better support two types of PS3 controller Also adding the option to use the 'Hat' buttons to control the Bot
2019-01-19 Adding Scratch motor control example
2019-05-18 A little code tidy up Adding some LED flashes to indicate program is starting when running without a monitor
2019-05-18 Fixing error FlashEDs not defined
    [ps3bot.py]
2019-05-18 LED output mode
2019-05-18 Fixing LED2 output
2019-05-25 Changing speed control to require the Select button to be pressed so that anyone with itchy trigger fingers don't accidentaly change the speed of their 'bot :o)
2019-09-21 Adding support for PiHut wireless PS3 controller clone Improving use of LEDs to indicate status
2019-09-21 Fixing speed adjustment controls
    [ps3bot.py]
